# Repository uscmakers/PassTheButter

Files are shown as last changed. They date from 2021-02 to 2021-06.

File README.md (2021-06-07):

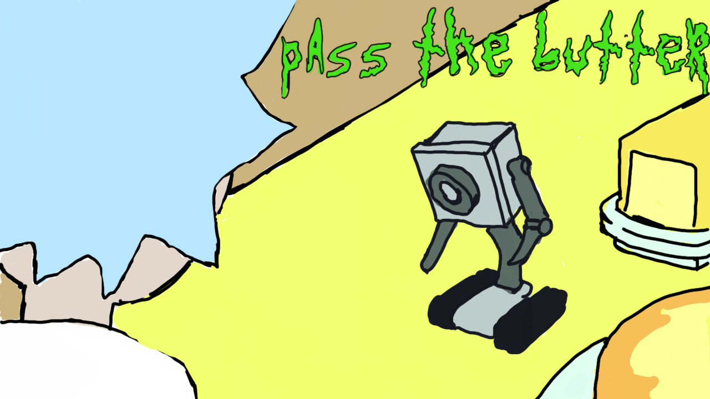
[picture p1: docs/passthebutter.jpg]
emily london logo


The purpose of this project is to build a robot which is capable of locating different people at a dinner table and passing butter to them when commanded. This is an idea made popular by a scene from Ricky and Morty.

[Here's our showcase video](https://youtu.be/vPM-rD34ycs?t=3011) describing the project, its purpose, its design, and the current state of affairs as of Spring 2021.

Full documentation can be found [here](docs/). This includes the original project plan (before work began), the bill of materials, the mechanical designs used for 3D printing, and the electronics schematics used for wiring. Electronics designs were made in [fritzing](https://fritzing.org/)

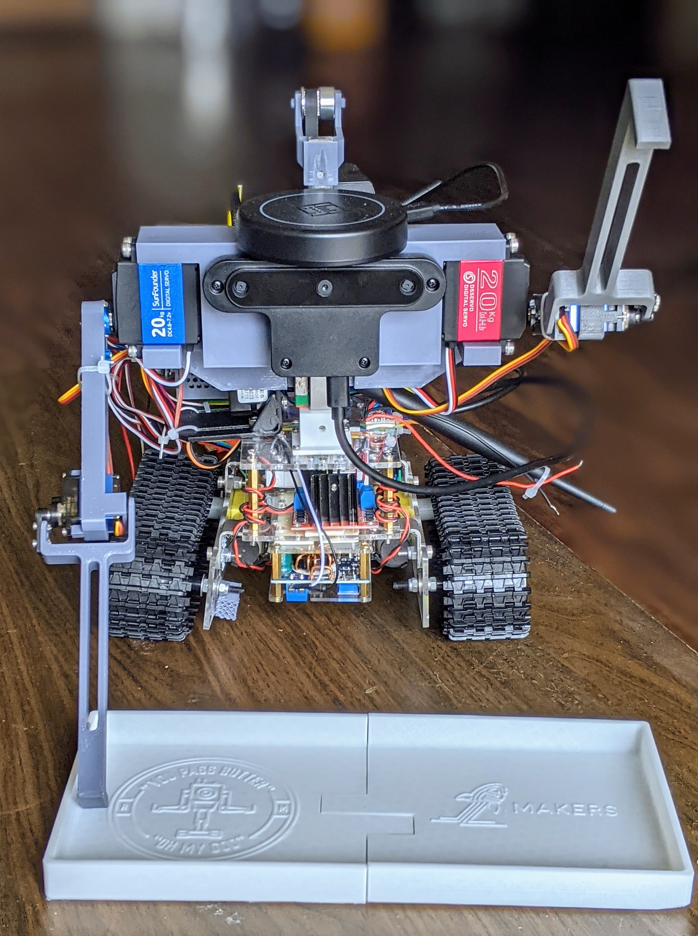
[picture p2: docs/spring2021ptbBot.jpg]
assembled robot spring 2021


# Setup

*The current version of this code expects ROS Melodic (Ubuntu 18.04) on a Jetson Nano 4GB. Many of the components will work on other platforms, but your mileage may vary, especially for things like circuit python.*

1. Wire everything up. [(See Jetson Nano pinout)](https://www.jetsonhacks.com/nvidia-jetson-nano-j41-header-pinout/)
1. [Ensure python/ROS can access your USB devices](https://askubuntu.com/questions/595896/how-to-allow-software-access-to-any-usb-devices) without admin permissions. [This may also help](https://askubuntu.com/questions/595896/how-to-allow-software-access-to-any-usb-devices).
1. [Setup circuit python on the Jetson Nano](https://learn.adafruit.com/circuitpython-libraries-on-linux-and-the-nvidia-jetson-nano/initial-setup)
1. Install ROS Melodic
1. Install pyaudio:
    ```bash
    sudo apt-get install libasound-dev portaudio19-dev libportaudio2 libportaudiocpp0
    sudo apt-get install ffmpeg libav-tools
    sudo python3 -m pip install pyaudio
    ```
1. Clone this repo to your ROS catkin_ws/src directory. 
1. `python3 -m pip install -r requirements.txt`
1. If using the wake word functionality, also do: `python3 -m pip install -r src/pass_butter/VoiceCommands/requirements.txt`
1. [Install the arduino rosserial package.](arduino/README.MD)
1. [Setup ROS for python3.](https://medium.com/@beta_b0t/how-to-setup-ros-with-python-3-44a69ca36674)
1. Build the pass_butter package with `catkin_make` or `catkin build`.

# Usage

The robot can be run in a few different ways right now, many at the same time as long as they do not use the same hardware. Take a look at the launch files and nodes especially. There remains some work to integrate all of this functionality into one or two scripts.

* If you would like to move the base around, then run this first (have it working in the background in addition to other nodes you launch): `roslaunch pass_butter arduino.launch` 
* To make the robot follow the direction of your voice run this: `rosrun pass_butter doa.py`
* To run the sequence of commands that was used for the demo video, call this `roslaunch pass_butter butter.launch`
* To view the URDF of the robot, run this: `roslaunch pass_butter rviz.launch`
* To make the robot respond to "computer" and play some response, run: `rosrun passbutter src/pass_butter/VoiceCommands/main.py --keywords computer`
* To get an interactive terminal for sending the robot commands, run this: `rosrun pass_butter demo.py`
  * 'u' - put arms up
  * 'd' - put arms down
  * 'w' - wave arms
  * 's#' - replace # with 0-4 to play different sounds
  * 'r###' - rotate the robot some amount, replace ### with a positive/negative decimal number
  * '###' - move forward or backward some amount, replace ### with a positive/negative decimal number
  * 'x' - exit/finish

## References

DOA: https://wiki.seeedstudio.com/ReSpeaker-USB-Mic-Array/#doa-direction-of-arrival

URDF: https://discourse.ros.org/t/fusion-360-add-in-to-export-urdf/6944
# Project Status

*Where does the project stand right now?*

## The Good 

1. The robot is fully assembled; the drive motors and arms are all functional. 
1. The robot has a working PID controller which is handled by an Arduino that communicates over ROS to the Jetson Nano.
1. The robot has a sense of wheel rotations and velocity thanks to the motor encoders
1. The robot can follow voice direction accurately using the directional microphone
1. The robot can respond to simple keywords such as "computer"

## The "Could Be Better"

1. Vertical head movement is non-functional. The stepper motor solution did not have enough torque to lift the relatively heavy head. The stepper motor is too weak. A worm gear motor would probably work much better with less hassle (stepper drivers can be annoying to setup).
1. The base is broken in multiple places and had to be glued back together on multiple occasions. The electronics hang off back of the base, and the base is bowing in the middle under the weight. A redesign of the base would be advisable to make it sturdier and to better fit all components.
1. The wiring is all done using a collection of breadboards and premade pcbs. This has led to some accidental short circuits of power wires. It would be much cleaner if it was all integrated to one main PCB.
1. We have an URDF to model the robot, but we do not yet have it integrated with the ROS transform system yet(e.g. [tf2](http://wiki.ros.org/tf2)) in order to view robot movement in rviz in real-time.
1. The arms do not have inverse kinematics setup--currently we work off of set points and known ranges of movement. Some calibration step would be useful too.
1. The arms can only pull or push, not grasp; more complex/useful arms would be interesting.
1. Full autonomy (obstacle avoidance, path planning) has not yet been setup/included in the software stack. The camera is currently not used.
1. Voice interaction is currently limited to wake words and does not make use of [dialogue/interaction systems](https://github.com/interaction-lab/HARMONI) which could provide much richer interactions without too much work.

# Contributors

 The project was led by a group of fantastic people who did a good amount of work in their spare time during a single semester. They are:

 * Anaka Mahesh
 * Avi Gala
 * Efaz Muhaimen (elctronics lead)
 * Max Ginsberg
 * Michael Swan (lead)
 * Misha Kuznetsov (mechanical lead)
 * Sam Jeon (autonomy lead)
 * Sarah Parks
 * Spencer Lin (voice interaction lead)

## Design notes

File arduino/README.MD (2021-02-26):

# Install Instructions

1. Install Arduino IDE
2. Get ROS Arduino libraries and install for ROS and Arduino:
```bash
sudo apt-get update
sudo apt-get install ros-melodic-rosserial-arduino
cd ~/Arduino/libraries
rosrun rosserial_arduino make_libraries.py .
```
3. Flash Arduino with provided code.
4. Start ros and run serial node communication (replace /dev/tty... with path matching your Arduino)
```bash
roscore
rosrun rosserial_python serial_node.py /dev/ttyACM0
```
5. Publish updates to the Arduino using ROS, e.g. `rostopic pub /servo std_msgs/UInt16 "data: 180"`

# References
http://wiki.ros.org/rosserial_arduino/Tutorials/Arduino%20IDE%20Setup

http://wiki.ros.org/rosserial_arduino/Tutorials/Blink

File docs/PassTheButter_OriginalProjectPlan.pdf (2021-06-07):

### Project Plan

1. Give a title for this project. (This can change later) Pass the Butter!
2. Describe the project in 2-3 sentences.

Build a robot which is capable of locating different people at a dinner table and passing butter to them when commanded. This is an idea made popular by a scene from Ricky and Morty. (https://youtu.be/X7HmltUWXgs?t=32) A toy is being produced (https://www.thebutterrobot.com/) for a similar purpose, but ours should be more customizable.

3. List the subsystems for this project and specify what each group will deliver by the end of the project.

Core subsystems
- Speaking: Shout out fun phrases when the robot engages in different actions.
- Listening: Listen to people and activate actions (e.g. passing butter) when certain key words are spoken. This subsystem must also provide the direction of spoken words (microphone arrays can do this).
- Butter Passing: Using either passive or active actuation, move butter around the table.
- Driving: Provide wheels, frame, and motors for rover to drive around upon. This can be done from scratch or by assembling a kit; that decision depends on available team members and interests.
- Obstacle Avoidance/Pathfinding: Avoid obstacles on the table and keep from falling off the table.

Possible extensions
- Conversing: Use Natural Language Understanding (NLU) to engage in a full conversation with people.
- Teleoperating: Control the robot and view its camera remotely using a computer, phone, or even Twitch chat. (https://www.twitch.tv/twitchplayspokemon)
- Voice Recognition: Identity the speaker using their voice, and then respond differently to different voices.
- Face Recognition: Same as voice recognition, except using faces.
- XYZ Passing: Pickup and move around other things (plates, trash, utensils, etc.) besides butter
4. How many people do you think you need on your team? Mention roles and skills if possible.

6-8 people, myself included (I fall into both the Computer/Software Engineer roles). We can support more software engineers (up to 6) if there are extra people available.

- 1-2 Mechanical Engineers to focus on robot body design/3D printing, motor placement, and actuator design for driving and butter passing.
- 2 Electrical/Computer Engineers to handle power distribution/wiring/pcb design and possibly help with some programming work.
- 3-4 Software Engineers to integrate and control all subsystems, with the bulk of their work being divided among the listening and obstacle avoidance subsystems.
5. List out parts your project will need, along with links for where to order them from.
a. [Already purchased] OAK-D AI + Depth Camera: https://www.kickstarter.com/projects/opencv/opencv-ai-kit
b. Speaker:
https://www.amazon.com/dp/B087D2BPBC/ref=cm_sw_em_r_mt_dp_6C T.FbAHCDT44 (https://www.amazon.com/dp/B087D2BPBC/ref=cm_sw_em_r_mt_dp_6CT.FbAHCDT44)
c. Microphone array (directional audio): https://www.digikey.com/short/477r2v
OR
https://www.seeedstudio.com/ReSpeaker-USB-Mic-Array-p-4247.html
d. Jetson nano:
https://www.amazon.com/dp/B084DSDDLT/ref=cm_sw_em_r_mt_dp_2I T.FbE0Y5RNH (https://www.amazon.com/dp/B084DSDDLT/ref=cm_sw_em_r_mt_dp_2IT.FbE0Y5RNH)
e. WiFi for Jetson nano:
https://www.amazon.com/dp/B07V9B5C6M/ref=cm_sw_em_r_mt_dp_oJ T.Fb4XAX22R (https://www.amazon.com/dp/B07V9B5C6M/ref=cm_sw_em_r_mt_dp_oJT.Fb4XAX22R)
f. Micro sd card:
https://www.amazon.com/dp/B08879MG33/ref=cm_sw_em_r_mt_dp_g5 T.FbC1ADJK3 (https://www.amazon.com/dp/B08879MG33/ref=cm_sw_em_r_mt_dp_g5T.FbC1ADJK3)
g. Jetson fan:
https://www.amazon.com/dp/B071FNHVXN/ref=cm_sw_em_r_mt_dp_85 T.FbS3C6MND (https://www.amazon.com/dp/B071FNHVXN/ref=cm_sw_em_r_mt_dp_85T.FbS3C6MND)
h. Jetson test bench Power Supply: https://www.amazon.com/dp/B07413Q5Y4
i. [Many Options, Choose 1] Motors + motor driver + chassis:
i. Jetbot kit https://www.adafruit.com/product/4225
ii. Tank Tread kit: https://smile.amazon.com/dp/B08F23SDF5/ref=cm_sw_em_r_mt_ dp_ZSJaGbBWMGKRD (https://smile.amazon.com/dp/B08F23SDF5/ref=cm_sw_em_r_mt_dp_ZSJaGbBWMGKRD)

iii. | Elegoo Kit
| https://smile.amazon.com/dp/B07KPZ8RSZ/ref=cm_sw_em_r_mt_
| dp_dlT1_rTJaGbBSVW61Z?_encoding=UTF8&psc=1 (https://smile.amazon.com/dp/B07KPZ8RSZ/ref=cm_sw_em_r_mt_dp_dlT1_rTJaGbBSVW61Z?_encoding=UTF8&psc=1)
iv. | Tank with arm kit:
| https://smile.amazon.com/dp/B07Q3RQCQS/ref=cm_sw_em_r_mt
| _dp_UTJaGbGKZDVG3 (https://smile.amazon.com/dp/B07Q3RQCQS/ref=cm_sw_em_r_mt_dp_UTJaGbGKZDVG3)
v. Osoyoo kit:
| https://smile.amazon.com/dp/B08JLS3J7Q/ref=cm_sw_em_r_mt_
| dp_AUJaGb61WHR82 (https://smile.amazon.com/dp/B08JLS3J7Q/ref=cm_sw_em_r_mt_dp_AUJaGb61WHR82)
vi. | 3-layer kit: https://www.adafruit.com/product/3244
j. Battery + regulators:
https://forums.developer.nvidia.com/t/power-supply-considerations-for-jetson-nano-developer-kit/71637/245 (https://forums.developer.nvidia.com/t/power-supply-considerations-for-jetson-nano-developer-kit/71637/245)
i. Most likely option: 2s LiPo battery with motor drivers provided by
| kit and possibly a 5V regulator and/or separate battery for the
| jetson; I already have a 2s LiPo
ii. | 5V Regulator (can work for servos and/or Jetson):
| https://www.amazon.com/dp/B00C63TLCC/ref=cm_sw_em_r_mt_
| dp_zvKaGbWTP4BB2 (https://www.amazon.com/dp/B00C63TLCC/ref=cm_sw_em_r_mt_dp_zvKaGbWTP4BB2)
k. Table edge detection (if not in kit): https://www.amazon.com/dp/B00XT0PBC0/ref=cm_sw_em_r_mt_dp_eb KaGbQN4BDSX (https://www.amazon.com/dp/B00XT0PBC0/ref=cm_sw_em_r_mt_dp_ebKaGbQN4BDSX)
l. Robot arm servos (MG90S): https://www.amazon.com/dp/B07FLXZ1VK/ref=cm_sw_em_r_mt_dp_lqK aGbN11ACJW (https://www.amazon.com/dp/B07FLXZ1VK/ref=cm_sw_em_r_mt_dp_lqKaGbN11ACJW)
m. Robot arm gripper: https://www.pololu.com/product/3551
6. Layout a timeline of the milestones that need to be completed to finish the project. Expect there to be 10-11 productive weeks to complete the project.
- Mid February: Robot prototype assembled and motors moving
- Mid March:
- Majority of mechanical/electrical body design/assembly (except arms) completed
- Table edge detection working
- Speaker working
- Mid April:
- Arms functional
- Microphone able to determine audio direction
- Obvious obstacles autonomously avoided using camera
- May (final): Able to pass butter from one side of table to the other using voice commands.

Embedded Plans/Considerations
- [Efaz] Using Fritzing for system connection diagram
- Don’t worry about circuit diagrams as much unless we add more small components
- 2 Arduino nanos, one for arms/servos, another for locomotion
- Arduinos communicate with Jetson Nano over serial (rosserial package)
- IMU contacts arduino over I2C

Jetson Nano Software Plans/Considerations:
- LucidChart for software package diagram: https://lucid.app/lucidchart/invitations/accept/1264b90b-86f0-4d57-a3e3-5235 82440beb (https://lucid.app/lucidchart/invitations/accept/1264b90b-86f0-4d57-a3e3-523582440beb)
- 30deg separation difference minimum needed for ultrasonic sensor to avoid interference
- Simplify arm IK by just doing it ourselves instead of integrating MoveIt: https://youtu.be/IN8tjTk8ExI
- What is the max speed we will set for our robot?

Mechanical Ideas/Plans:
- Linear rail MGN12 H (150 mm) for vertical cam movement provided by Spencer: https://www.aliexpress.com/item/32806622073.html?spm=a2g0s.9042311.0.0.27 424c4dN0Uh1O
- Using black micro servos for arms.
- 2 arms if possible, but otherwise only one.
- Could get higher torque even: https://www.adafruit.com/product/2307
- Gripper for arm that uses micro servo: https://www.pololu.com/product/3551
- Potential drive train depends on size of nano + other parts
- https://www.amazon.com/dp/B08F23SDF5/ref=cm_sw_em_r_mt_dp_ZSJaGbBWMGKRD?pldnSite=1 (https://www.amazon.com/dp/B08F23SDF5/ref=cm_sw_em_r_mt_dp_ZSJaGbBWMGKRD?pldnSite=1)
- https://www.amazon.com/DGJYT-Preminum-Raspberry-Learning-Caterpillar/dp/B08HSTC96H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 (https://www.amazon.com/DGJYT-Preminum-Raspberry-Learning-Caterpillar/dp/B08HSTC96H)
- https://www.amazon.com/Experiment-Programable-Platform-Compatible-Raspberry/dp/B0892YJ3KQ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 psc=1&refRID=W7JTG1CQZ3TFHQY6RTX0 (https://www.amazon.com/Experiment-Programable-Platform-Compatible-Raspberry/dp/B0892YJ3KQ)

- Could consider 3D printing something from Thingiverse
■ https://www.thingiverse.com/thing:2024364
■
- Motors with encoders: https://www.dfrobot.com/product-1457.html
- Max’s servo:
https://www.amazon.com/SunFounder-Waterproof-SF3218MG-Digital-Aluminium/dp/B07VJG5QTJ (https://www.amazon.com/SunFounder-Waterproof-SF3218MG-Digital-Aluminium/dp/B07VJG5QTJ)
- Micro servos:
- https://www.adafruit.com/product/2307
- https://www.adafruit.com/product/1143 ●

●

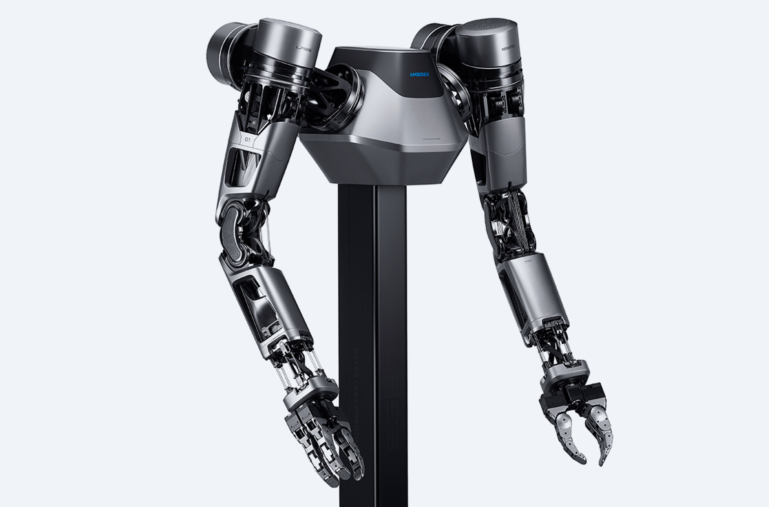
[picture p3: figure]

Reference Projects
1. Cliff detection and collision avoidance using IR sensors
- https://www.youtube.com/watch?v=d7J0Bb78y2s
- https://www.youtube.com/watch?v=BLYP94Yk12U
- https://www.youtube.com/watch?v=lN9uT30YzAg
●

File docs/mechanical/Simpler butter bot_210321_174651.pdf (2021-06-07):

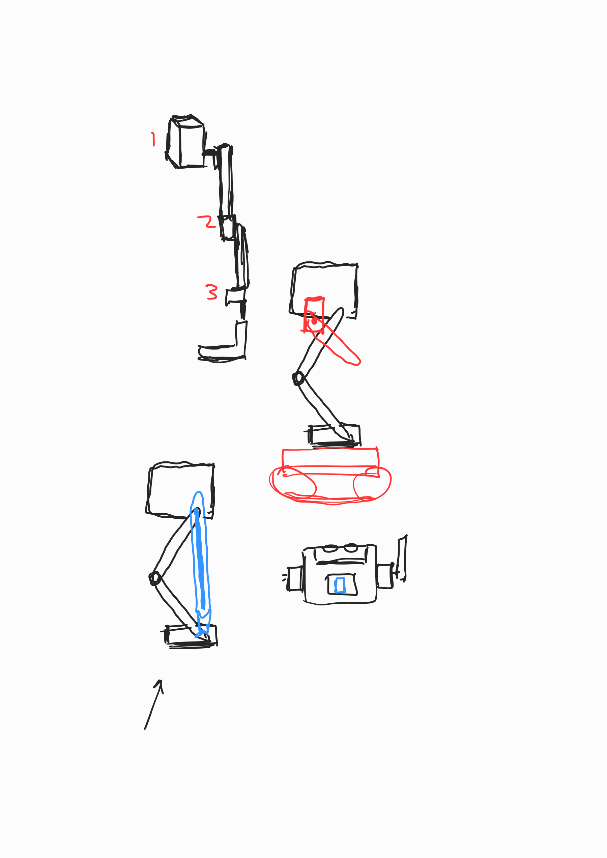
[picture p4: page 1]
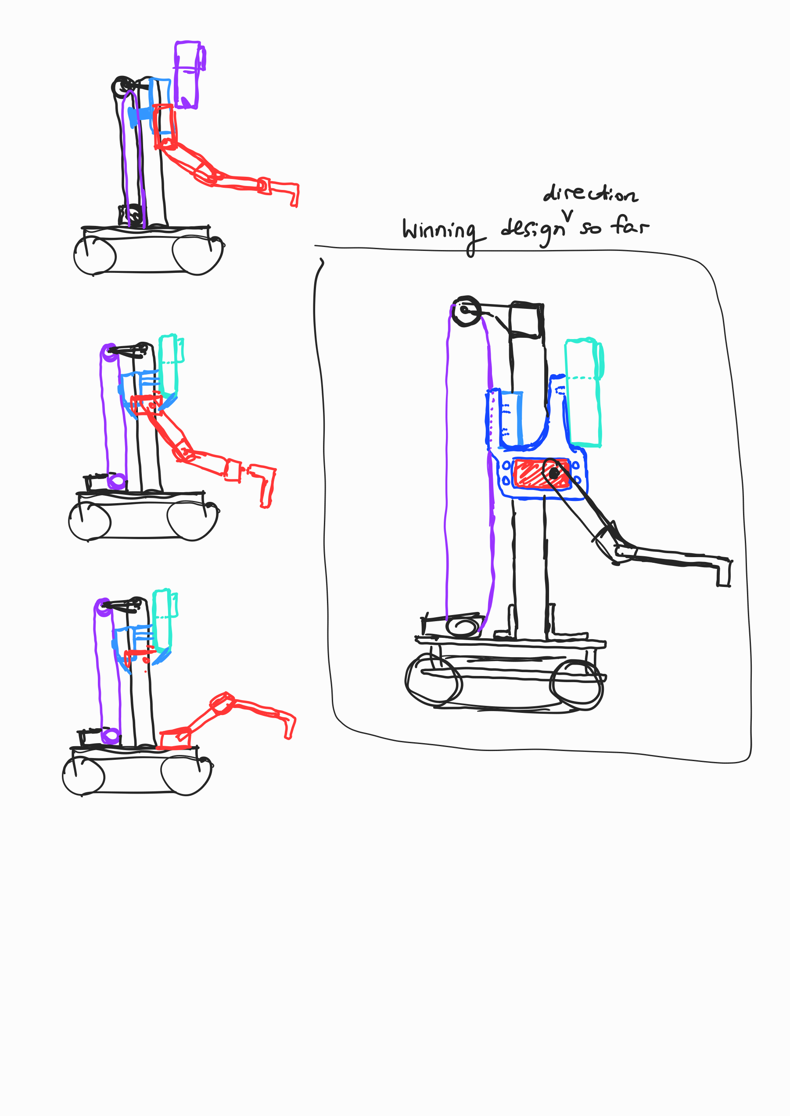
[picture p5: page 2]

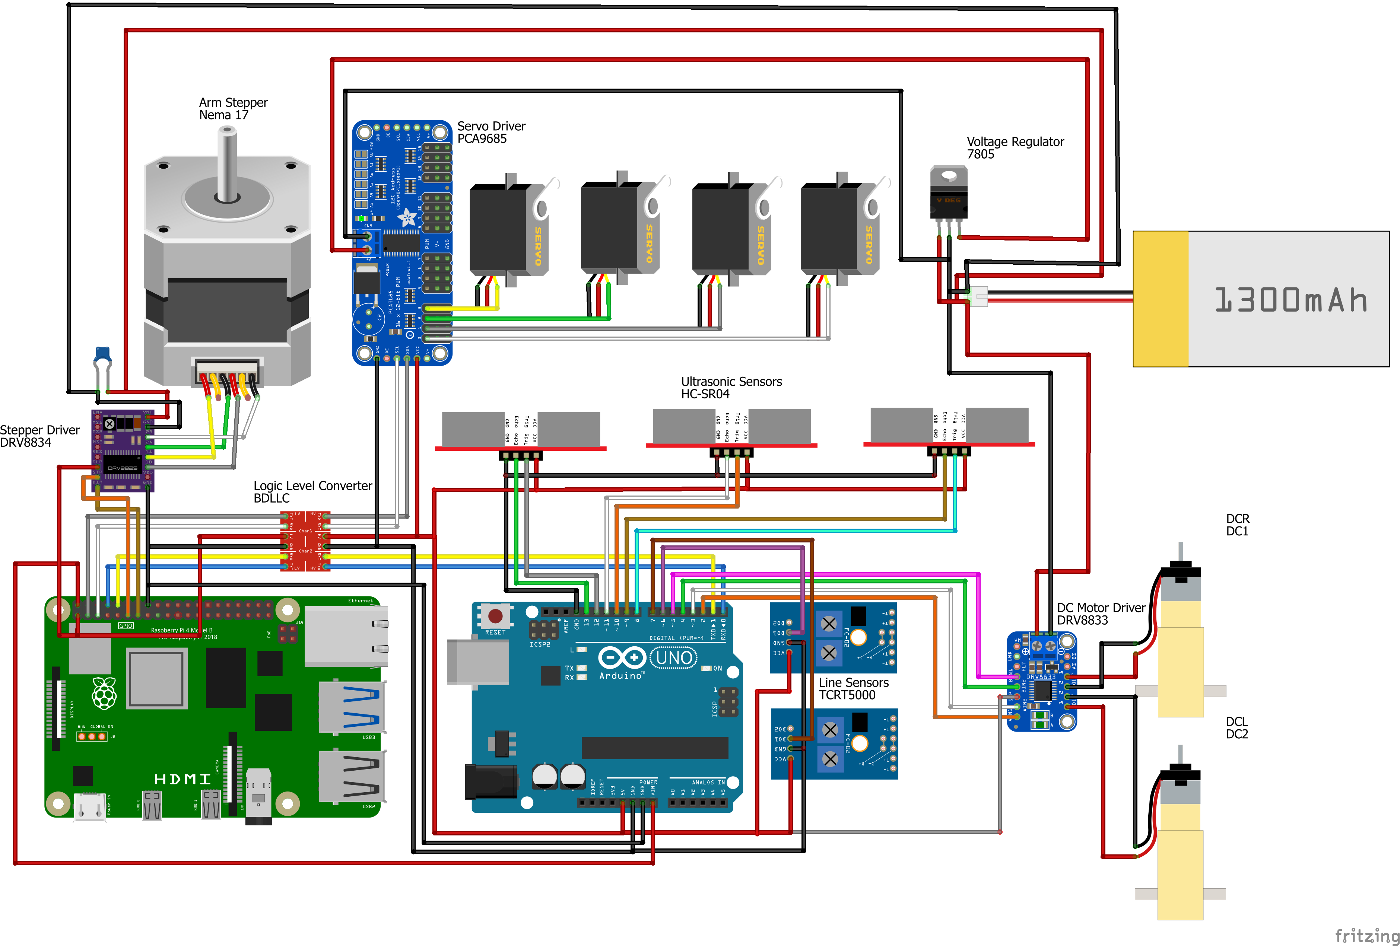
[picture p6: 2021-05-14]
docs/electronics/Schematic.png

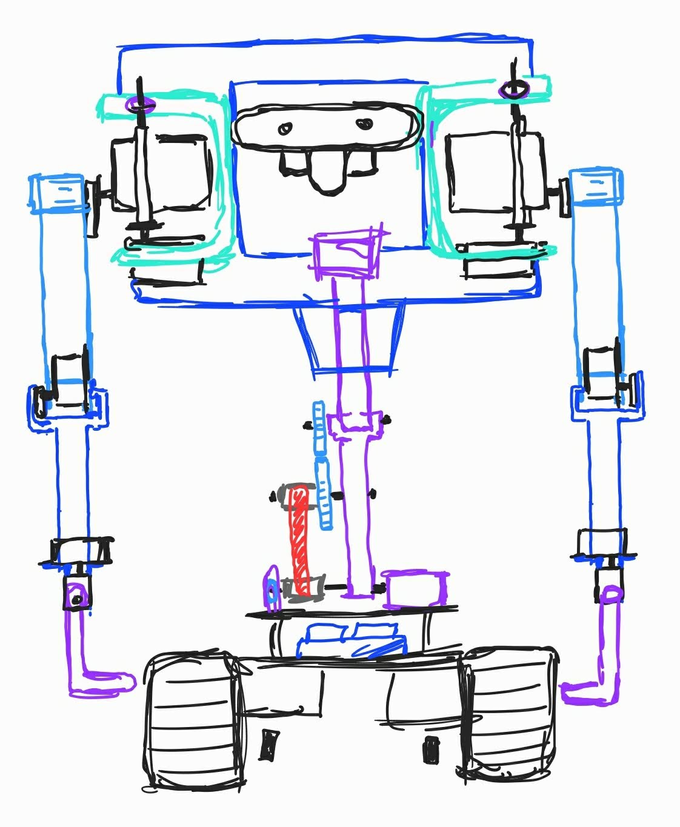
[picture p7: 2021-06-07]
docs/mechanical/SmartSelect_20210307-023447_Samsung Notes.jpg

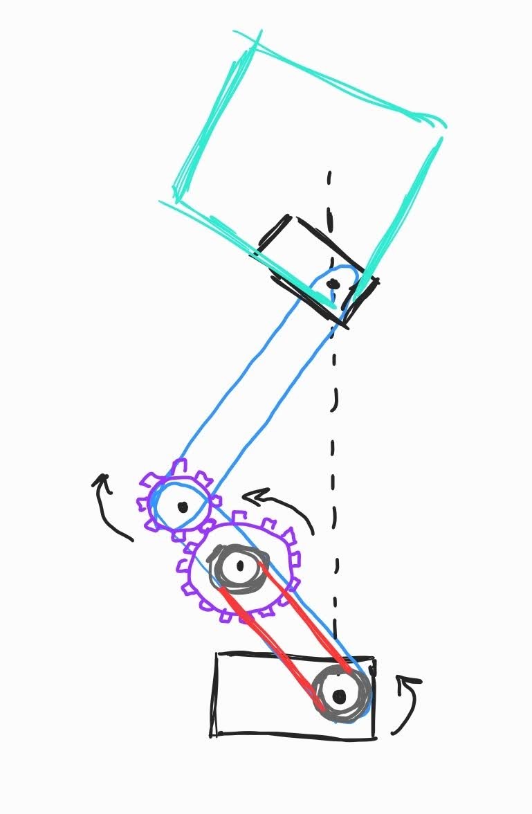
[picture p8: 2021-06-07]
docs/mechanical/SmartSelect_20210307-014712_Samsung Notes.jpg

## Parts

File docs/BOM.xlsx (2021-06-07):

Category | State | Part Name | Part Description | Make/Buy | QTY | Unit Cost | Shipping | Cost (excl tax + shipping) | Final Cost (incl tax + shipping)) | Vendor | Vendor URL | Comments
Electronics | Purchased | Jetson Nano 4GB |  |  | 1 | $84.99 | Prime - free | $84.99 | $93.06 |  | https://www.amazon.com/dp/B084DSDDLT/ref=cm_sw_em_r_mt_dp_7MWT5MMYDYXTCAPRW6YM
Electronics | Purchased | Jetson Nano Wifi Adapter |  |  | 1 | $24.25 | Prime - free | $24.25 | $26.55 |  | https://www.amazon.com/dp/B07V9B5C6M/ref=cm_sw_em_r_mt_dp_oJT.Fb4XAX22R
Electronics | Purchased | Noctua NF-A4x20 5V PWM | Fan for Jetson Nano |  | 1 | $14.95 | Prime - free | $14.95 | $16.37 |  | https://www.amazon.com/dp/B071FNHVXN/ref=cm_sw_em_r_mt_dp_85T.FbS3C6MND
Electronics | Purchased | 64 gb microSD card | for Jetson Nano |  | 1 | $10.99 | Prime - free | $10.99 | $12.03 |  | https://www.amazon.com/dp/B08879MG33/ref=cm_sw_em_r_mt_dp_g5T.FbC1ADJK3
Electronics | Purchased | Geekworm DC 5V 4A Power Adapter | AC Power supply for Nano |  | 1 | $17.99 | Prime - free | $17.99 | $19.70 |  | https://www.amazon.com/dp/B07413Q5Y4
Electronics | Have | Ultrasonic Sensor |  |  | 1 set (3 pieces) | $7.99 | Prime - free | $7.99 | $8.75 |  | https://www.amazon.com/Excelity-Ultrasonic-HC-SR04-Distance-Mounting/dp/B07SC1YJ21
Electronics | Tentative | Infrared Sensor |  |  | 1 set (5 pieces) | $5.49 | Prime - free | $5.49 | $6.01 |  | https://www.amazon.com/dp/B00XT0PBC0/ref=cm_sw_em_r_mt_dp_ebKaGbQN4BDSX
Electronics | Have | Motor+Encoder |  |  | 2 | $7.40 |  | $14.80 | $16.20 |  | https://www.dfrobot.com/product-1457.html
Mechanical | Purchased | 6Pcs MG90S Micro Servo |  |  | 1 set (6 pcs) | $18.99 | Prime - free | $18.99 | $20.79 | amazon | https://www.amazon.com/Seamuing-MG90S-Micro-Geared-Helicopter/dp/B07F7VJQL5/
 |  |  |  |  |  |  |  | $0.00 | $0.00
Mechanical | Purchased | Higher torque micro servo |  |  | 2 | $11.95 | $5.10 | $23.90 | $31.27 |  | https://www.adafruit.com/product/2307
Mechanical | Purchased | Drive Base |  |  | 1 | $27.90 | Prime - free | $27.90 | $30.55 | amazon | https://www.amazon.com/dp/B08F23SDF5/ref=cm_sw_em_r_mt_dp_ZSJaGbBWMGKRD?pldnSite=1
Mechanical | Purchased | 2 20KG Servo |  |  | 1 set (2 pcs) | $30.99 | Prime - free | $30.99 | $33.93 |  | https://www.amazon.com/DS3218-Digital-Servo-Torque-Waterproof/dp/B07TKTQ2NZ
Electronics | Have | Arduinos |  |  | 1 set (3 pcs)
Electronics | Purchased | DRV8833 DC Motor Driver |  |  | 1 | $8.91 | Prime - free | $8.91 | $9.76 |  | https://www.amazon.com/Adafruit-DRV8833-Stepper-Driver-Breakout/dp/B01MFE1CZU/
Electronics | Purchased | ReSpeaker USB Mic Array |  |  | 1 | $69.00 | $6.32 | $69.00 | $75.32 |  | https://www.seeedstudio.com/ReSpeaker-USB-Mic-Array-p-4247.html
Electronics | Purchased | USB Speaker |  |  | 1 | $19.99 | Prime - free | $19.99 | $21.89 |  | https://www.amazon.com/dp/B087D2BPBC/ref=cm_sw_em_r_mt_dp_6CT.FbAHCDT44
Electronics | Purchased | Diymore 6DOF MPU-6050 |  |  | 1 | $6.90 | Prime - free | $6.90 | $7.55 |  | https://www.amazon.com/dp/B01J167T84/ref=cm_sw_em_r_mt_dp_B9NT7TBK1H0HZQJKAH9Y?_encoding=UTF8&psc=1
Electronics | Purchased | Logic Level Converter |  |  | 1 | $7.49 | Prime - free | $7.49 | $8.20 |  | https://www.amazon.com/HiLetgo-Channels-Converter-Bi-Directional-3-3V-5V/dp/B07F7W91LC/
Mechancial | Purchased | Stepper Motor Nema 17 |  |  | 1 | $9.99 | Prime - free | $9.99 | $10.94 | amazon | https://www.amazon.com/Twotrees-Stepper-17HS4401-Connector-Printer/dp/B07TGJSNJB
Mechanical | Purchased | Stepper Motor Bracket |  |  | 1 | $5.99 | Prime - free | $5.99 | $6.56 | amazon | https://www.amazon.com/STEPPERONLINE-Mounting-Bracket-Stepper-Printer/dp/B00Q6F51C0
Mechancial | Purchased | Pulleys |  |  | 1 | $8.98 | Prime - free | $8.98 | $9.83 | amazon | https://www.amazon.com/gp/product/B077GNZK3J/ref=ppx_yo_dt_b_search_asin_title?ie=UTF8&th=1
Mechancial | Purchased | Belts |  |  | 1 | $10.99 | Prime - free | $10.99 | $12.03 | amazon | https://www.amazon.com/Houkr-Printer-Timing-Closed-Perimeter/dp/B085NMDTDM
Electronics | Purchased | Voltage Regulator |  |  | 1 | $13.99 | Prime - free | $13.99 | $15.32 |  | https://www.amazon.com/AITRIP-Adjustable-Regulator-Transformer-Converter/dp/B08FJ2GGQN/
Electronics | Purchased | Servo Driver |  |  | 1 | $9.99 | Prime - free | $9.99 | $10.94 |  | https://www.amazon.com/SunFounder-PCA9685-Channel-Arduino-Raspberry/dp/B014KTSMLA/
Electronics | Purchased | Stepper Driver |  |  | 1 | $5.95 | $4.33 | $5.95 | $10.84 | Pololu | https://www.pololu.com/product/2134
Electronics | tentative | Voltage Sensor |  |  | 1 | $13.74 | Prime - free | $13.74 | $15.04 |  | https://www.amazon.com/Adafruit-INA260-Voltage-Current-Sensor/dp/B07S8QYDF8/
Electronics | Have | OAK-D Camera |  |  | 1 | $149 | $16 | $149 | $165.00 |  | https://store.opencv.ai/products/oak-d
Mechanical | Have | MGN 12H 150mm Linear Rail |  |  | 1 | $10.13 |  |  |  |  | https://www.aliexpress.com/item/32806622073.html?spm=a2g0s.9042311.0.0.27424c4dN0Uh1O
 |  |  |  |  |  |  |  |  | Purchased so far
 |  |  |  |  |  |  |  |  | $483.42
 |  |  |  |  |  |  |  |  | Everything Total
 |  |  |  |  |  |  |  |  | $694.43

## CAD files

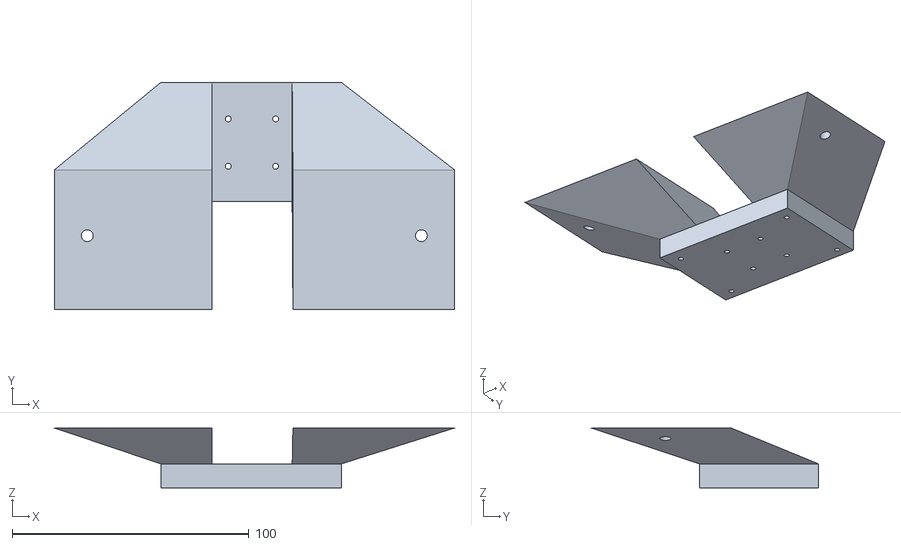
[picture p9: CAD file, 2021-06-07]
docs/mechanical/body2mmholes.stl
168.8 x 95.9 x 25.3

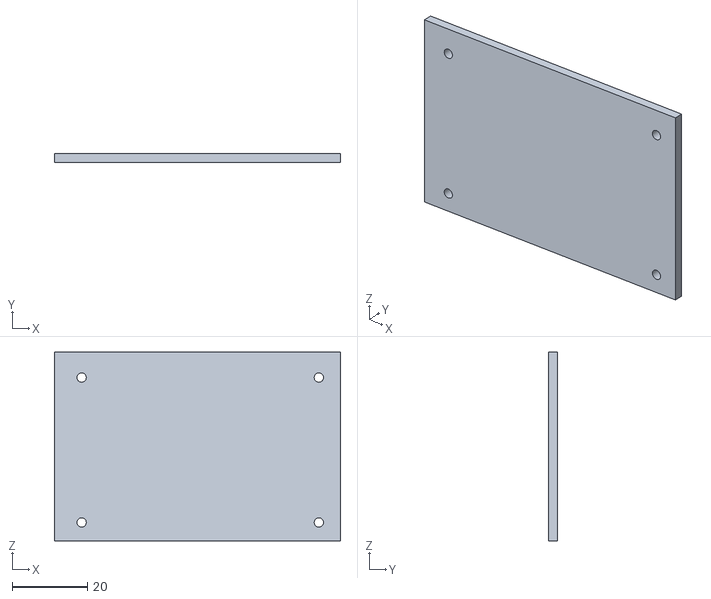
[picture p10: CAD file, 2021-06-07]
docs/mechanical/body3mmholes.stl
76.2 x 2.34 x 50.3

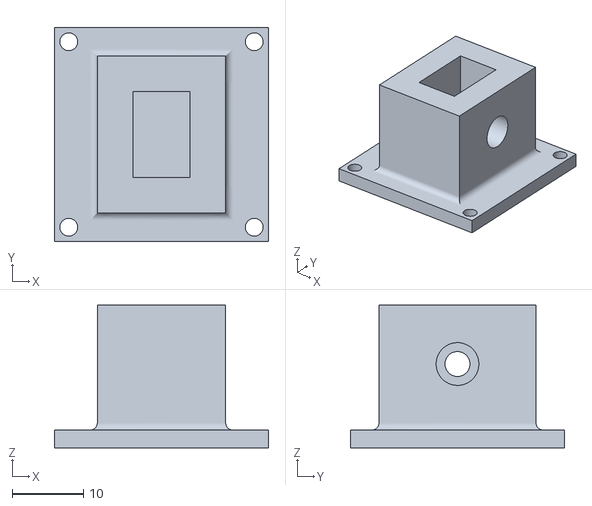
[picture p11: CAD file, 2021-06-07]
docs/mechanical/Bracket v1.stl
30.0 x 30.0 x 20.0

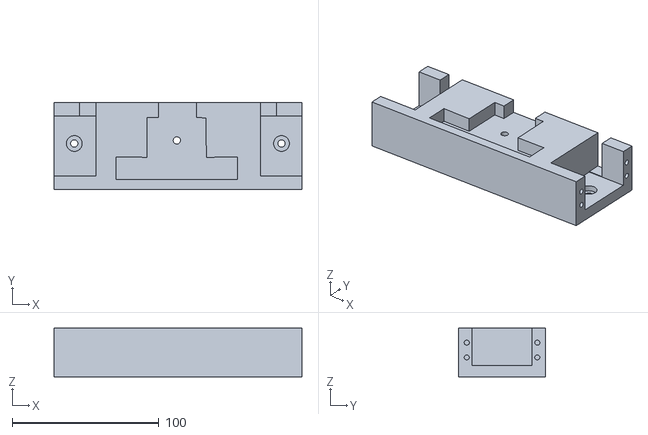
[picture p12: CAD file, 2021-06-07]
docs/mechanical/bigboyholes.stl
168.8 x 59.0 x 33.0

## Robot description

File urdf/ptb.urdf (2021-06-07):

<?xml version="1.0"?>
<robot name="test_robot">

  <link name="base_link">
    <visual>
      <geometry>
        <box size="0.5 0.3 0.05"/>
      </geometry>
      <origin rpy="0 0 0" xyz="0 0 0.085"/>
      <material name="white">
        <color rgba="1 1 1 1"/>
      </material>
    </visual>
  </link>
  
  <link name="lfwheel">
    <visual>
      <geometry>
        <cylinder length="0.008" radius="0.046"/>
      </geometry>
      <origin rpy="1.5708 0 0" xyz="0 0 0"/>
      <material name="black">
        <color rgba="0 0 0 1"/>
      </material>
    </visual>
  </link>
  
  <joint name="base_to_lfwheel" type="continuous">
    <parent link="base_link"/>
    <child link="lfwheel"/>
    <axis rpy="0 0 0" xyz="0 1 0"/>
    <origin xyz=".2 0.16 0.046" rpy="0 0 0"/>
  </joint>
  

 <link name="lbwheel">
    <visual>
      <geometry>
        <cylinder length="0.008" radius="0.046"/>
      </geometry>
      <origin rpy="1.5708 0 0" xyz="0 0 0"/>
      <material name="black">
        <color rgba="0 0 0 1"/>
      </material>
    </visual>
  </link>
  
  <joint name="base_to_lbwheel" type="continuous">
    <parent link="base_link"/>
    <child link="lbwheel"/>
    <axis rpy="0 0 0" xyz="0 1 0"/>
    <origin xyz="-.2 0.16 0.046" rpy="0 0 0"/>
  </joint>
  

  <link name="rfwheel">
    <visual>
      <geometry>
        <cylinder length="0.008" radius="0.046"/>
      </geometry>
      <origin rpy="1.5708 0 0" xyz="0 0 0"/>
      <material name="black">
        <color rgba="0 0 0 1"/>
      </material>
    </visual>
  </link>
  
  <joint name="base_to_rfwheel" type="continuous">
    <parent link="base_link"/>
    <child link="rfwheel"/>
    <axis rpy="0 0 0" xyz="0 1 0"/>
    <origin xyz= ".2 -0.16 0.046" rpy="0 0 0"/>
  </joint>

 <link name="rbwheel">
    <visual>
      <geometry>
        <cylinder length="0.008" radius="0.046"/>
      </geometry>
      <origin rpy="1.5708 0 0" xyz="0 0 0"/>
      <material name="black">
        <color rgba="0 0 0 1"/>
      </material>
    </visual>
  </link>
  
  <joint name="base_to_rbwheel" type="continuous">
    <parent link="base_link"/>
    <child link="rbwheel"/>
    <axis rpy="0 0 0" xyz="0 1 0"/>
    <origin xyz="-.2 -0.16 0.046" rpy="0 0 0"/>
  </joint>

  <link name="post">
    <visual>
      <geometry>
        <box size=".03 .03 .4"/>
      </geometry>
      <origin rpy="0 0 0" xyz="0 0 .2"/>
      <material name="black">
        <color rgba="0 0 0 1"/>
      </material>
    </visual>
  </link>

  <joint name="post_to_chassis" type="fixed">
    <parent link="base_link"/>
    <child link="post"/>
    <origin xyz=".2 0 .1" rpy="0 0 0"/>
  </joint>
 
  <link name="cross">
    <visual>
      <geometry>
        <box size=".03 .3 .03"/>
      </geometry>
      <origin rpy="0 0 0" xyz="0 0 0"/>
      <material name="black">
        <color rgba="0 0 0 1"/>
      </material>
    </visual>
  </link>

  <joint name="cross_to_post" type="prismatic">
    <parent link="post"/>
    <child link="cross"/>
    <axis xyz="0 0 1"/>
     <limit effort="1000.0" lower="-.2" upper="0" velocity="0.5"/>
    <origin xyz="0 0 .3" rpy="0 0 0"/>
  </joint>



  <link name="upper_arm_l">
    <visual>
      <geometry>
        <box size=".15 .03 .03"/>
      </geometry>
      <origin rpy="0 0 0" xyz=".05 0 0"/>
      <material name="white">
        <color rgba="0 0 0 0"/>
      </material>
    </visual>
  </link>

  <joint name="upper_arm_l_to_cross" type="revolute">
    <parent link="cross"/>
    <child link="upper_arm_l"/>
    <axis xyz="0 1 0"/>
    <limit effort="1000.0" lower="0.0" upper="-0.7" velocity="0.5"/>
    <origin xyz="0 .17 0" rpy="0 0 0"/>
  </joint>

  <link name="forearm_l">
    <visual>
      <geometry>
        <box size=".15 .03 .03"/>
      </geometry>
      <origin rpy="0 0 0" xyz="0.06 0 0"/>
      <material name="black">
        <color rgba="0 0 0 1"/>
      </material>
    </visual>
  </link>

  <joint name="forearm_l_to_upper_arm_l" type="revolute">
    <parent link="upper_arm_l"/>
    <child link="forearm_l"/>
    <axis xyz="0 1 0"/>
   <limit effort="1000.0" lower="0.0" upper="-0.7" velocity="0.5"/>
    <origin xyz=".1 .035 0" rpy="0 0 0"/>
  </joint>

  <link name="upper_arm_r">
    <visual>
      <geometry>
        <box size=".15 .03 .03"/>
      </geometry>
      <origin rpy="0 0 0" xyz=".05 0 0"/>
      <material name="white">
        <color rgba="0 0 0 0"/>
      </material>   
    </visual>
  </link>

  <joint name="upper_arm_r_to_cross" type="revolute">
    <parent link="cross"/>
    <child link="upper_arm_r"/>
    <axis xyz="0 1 0"/>
    <limit effort="1000.0" lower="0.0" upper="-0.7" velocity="0.5"/>
    <origin xyz="0 -.17 0" rpy="0 0 0"/>
  </joint>

  <link name="forearm_r">
    <visual>
      <geometry>
        <box size=".15 .03 .03"/>
      </geometry>
      <origin rpy="0 0 0" xyz=".06 0 0"/>
      <material name="black">
        <color rgba="0 0 0 1"/>
      </material>
    </visual>
  </link>

  <joint name="forearm_r_to_upper_arm_r" type="revolute">
    <parent link="upper_arm_r"/>
    <child link="forearm_r"/>
    <axis xyz="0 1 0"/>
    <limit effort="1000.0" lower="0.0" upper="-0.7" velocity="0.5"/>
    <origin xyz=".1 -.035 0" rpy="0 0 0"/>
  </joint>
  
</robot>

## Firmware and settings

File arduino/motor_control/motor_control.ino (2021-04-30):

#include <PID_v1.h> // PID library
#include <ros.h> // ROS serial
#include <ros/time.h>
#include "Wire.h" // IMU wire library
#include "I2Cdev.h"
#include <geometry_msgs/Vector3.h> 
#include <tf/transform_broadcaster.h>
#include <MPU6050.h> // MPU 6050 IMU library

MPU6050 mpu;

//Create an object that represents the ROS node
ros::NodeHandle nh;

//Create sensor messages
geometry_msgs::TransformStamped t; 
geometry_msgs::TransformStamped t2;
tf::TransformBroadcaster broadcaster;

//Encoders
const byte encoder0pinA = 2;// A pin for motor 1
const byte encoder0pinB = 4;// B pin for motor 1

const byte encoder1pinA = 3;// A pin for motor 2
const byte encoder1pinB = 5;// B pin for motor 2

byte encoder0PinALast; // Last encoder reading for motor 1
byte encoder1PinALast; // Last encoder reading for motor 2

double duration1; // Pulses/sec for the encoder in motor 1
double duration2; // Pulses/sec for the encoder in motor 2

double abs_duration1, abs_duration2; // Speed for motor 1 and 2

//Motor PWM
double PWM1, PWM2; // PWM signals for motor 1 and motor 2

double set1, set2 = 0; // Velocity set points for motor 1 and motor 2
double setanglespeed; // Angular speed set point
double setspeed; // Net speed

int r = 0.035; // Wheel radius (m)
int l = 0.11 ; // Robot track width (m)

boolean Direction1; // Motor 1 direction
boolean Direction2; // Motor 2 direction

const int ENA = 6; // Motor1 output pin
const int IN1 = 7; // Motor1 direction pin 1
const int IN2 = 8; // Motor1 direction pin 2

const int ENB = 11; // Motor2 output pin
const int IN3 = 9; // Motor2 direction pin 1
const int IN4 = 10; // Motor2 direction pin 2

//IMU
float yaw, yawRate,xAcc,yAcc = 0;
float timeStep = 0.01;

float read1 = 0;
float read2 = 0;

char world[] = "world";
char imu[] = "/imu";


// Timers
unsigned long timer, range_timer = 0;

double set = 0; // Setpoint speed -- I guess will be given order from ROS
double val_output; // PWM output
double Kp=0.6, Ki=3.8, Kd=0; // PID gains
PID myPID1(&abs_duration1, &PWM1, &set1, Kp, Ki, Kd, DIRECT); // PID setup for motor 1
PID myPID2(&abs_duration2, &PWM2, &set1, Kp, Ki, Kd, DIRECT); // PID setup for motor 1
boolean result1, result2; // PID control outcome

void setup()
{
  nh.initNode();
  broadcaster.init(nh); 

  // Initialize MPU6050
  while(!mpu.begin(MPU6050_SCALE_2000DPS, MPU6050_RANGE_2G))
  {
    Serial.println("Could not find a valid MPU6050 sensor, check wiring!");
    delay(500);
  }
  
  // Calibrate gyroscope. The calibration must be at rest.
  // If you don't want calibrate, comment this line.
  mpu.calibrateGyro();

  // Set threshold sensivty. Default 3.
  // If you don't want use threshold, comment this line or set 0.
  mpu.setThreshold(3);
  
  // Motor driver setup
  pinMode(IN1, OUTPUT);
  pinMode(IN2, OUTPUT);
  pinMode(ENA, OUTPUT);
  pinMode(IN3, OUTPUT);
  pinMode(IN4, OUTPUT);
  pinMode(ENB, OUTPUT);

  // Encoder initialization
  EncoderInit();

  // PID setup
  myPID1.SetMode(AUTOMATIC);// PID is set to automatic mode
  myPID1.SetSampleTime(50);// PID sampling every 0.05 seconds
  myPID2.SetMode(AUTOMATIC);// PID is set to automatic mode
  myPID2.SetSampleTime(50);// PID sampling every 0.05 seconds
}

void loop()
{
  //Serial.print("Pulse:");
  //Serial.println(duration1);
  //Serial.print("Pulse:");
  //Serial.println(duration2);
  abs_duration1=abs(duration1);
  abs_duration2=abs(duration2);
  result1=myPID1.Compute();
  result2=myPID2.Compute();
  if(result1 && result2)
  {

    duration1, duration2 = 0; //Count clear, wait for the next count
    }
  timer = millis();
  Vector normGyro = mpu.readNormalizeGyro();
  Vector normAccel = mpu.readNormalizeAccel();
  
  if ( (millis()-range_timer) > 50){
    yaw = yaw+normGyro.ZAxis*(millis()-range_timer)*0.001;
    t.header.frame_id = world;
    t.child_frame_id = imu;
    t.transform.rotation.w = cos((yaw/2));
    t.transform.rotation.z = sin((yaw/2));
    t.transform.rotation.y = 0;
    t.transform.rotation.x = 0;
    t.header.stamp = nh.now();
    broadcaster.sendTransform(t); 

    range_timer = millis();
    }
    nh.spinOnce();
}

void EncoderInit()
{
  Direction1 = true;//default -> Forward
  Direction2 = true;
  pinMode(encoder0pinB,INPUT);
  attachInterrupt(1, wheelSpeed1, CHANGE);
  attachInterrupt(0, wheelSpeed2, CHANGE);
}

void wheelSpeed1()
{
  int Lstate1 = digitalRead(encoder0pinA);
  if((encoder0PinALast == LOW) && Lstate1==HIGH)
  {
    int val1 = digitalRead(encoder0pinB);
    if(val1 == LOW && Direction1)
    {
      Direction1 = false; //Reverse
    }
    else if(val1 == HIGH && !Direction1)
    {
      Direction1 = true;  //Forward
    }
  }
  encoder0PinALast = Lstate1;

  if(!Direction1){
    duration1--;
  }
  else{
    duration1++;
  }
}

void wheelSpeed2()
{
  int Lstate2 = digitalRead(encoder1pinA);
  if((encoder1PinALast == LOW) && Lstate2==HIGH)
  {
    int val2 = digitalRead(encoder1pinB);
    if(val2 == LOW && Direction2)
    {
      Direction2 = false; //Reverse
    }
    else if(val2 == HIGH && !Direction2)
    {
      Direction2 = true;  //Forward
    }
  }
  encoder1PinALast = Lstate2;

  if(!Direction2){
    duration2++;
  }
  else{
    duration2--;
  }
}

// Motor 1 command
void move_motor1()
{
    // Saturation: Max PWM = 255 and Min PWM = -255
    if (PWM1>255){
      PWM1 = 250;
    }

    else if(PWM1<-255){
      PWM1 = -250;
    }

     // PWM + Direction
     analogWrite(ENA,PWM1);
     digitalWrite(IN1,HIGH);
     digitalWrite(IN2,LOW);
}

// Motor 2 command
void move_motor2()
{
    // Saturation: Max PWM = 255 and Min PWM = -255
    if (PWM2>255){
      PWM2 = 250;
    }

    else if(PWM2<-255){
      PWM2 = -250;
    }

     // PWM + Direction
     analogWrite(ENB,PWM2);
     digitalWrite(IN3,HIGH);
     digitalWrite(IN4,LOW);
}

void calculate(double thetadot, double setspeed){
  
}

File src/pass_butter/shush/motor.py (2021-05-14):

__author__ = 'ZJAllen'

from shush.board import Board, s1, gpio
from shush.drivers import tmc5160_reg as reg
import time

from shush.params import Ramp as ramp


class Motor(Board):

    def __init__(self, motor: int):
        # Setting the CS and enable pins according to the motor number called

        if motor == 0:
            self.chip_select = s1.m0_cs
            self.enable = s1.m0_enable

        # Initially apply default settings.
        # These can be configured at any time.
        self.default_settings()

    def enable_motor(self):
        # Pull Enable pin LOW to enable motor

        gpio.output(self.enable, gpio.LOW)

    def disable_motor(self):
        # Pull Enable pin HIGH to disable motor

        gpio.output(self.enable, gpio.HIGH)

    def default_settings(self):
        # Set default motor parameters

        # MULTISTEP_FILT = 1, EN_PWM_MODE = 1 enables stealthChop
        self.write(reg.GCONF, 0x0000000C)
        # TOFF = 3, HSTRT = 4, HEND = 1, TBL = 2, CHM = 0 (spreadCycle)
        self.write(reg.CHOPCONF, 0x000100C3)
        # IHOLD = 2, IRUN = 15 (max current), IHOLDDELAY = 8
        self.write(reg.IHOLD_IRUN, 0x00080F02)
        # TPOWERDOWN = 10: Delay before powerdown in standstill
        self.write(reg.TPOWERDOWN, 0x0000000A)
        # TPWMTHRS = 500
        self.write(reg.TPWMTHRS, 0x000001F4)

        self.reset_ramp_defaults()

        # Position mode
        self.write(reg.RAMPMODE, 0)
        # Set current position to 0
        self.write(reg.XACTUAL, 0)
        # Set XTARGET to 0, which holds the motor at the current position
        self.write(reg.XTARGET, 0)

    # TODO: add some more functionality...
    # Add stallGuard + coolStep (datasheet page 52)

    def set_VSTART(self, value: int):
        self.write(reg.VSTART, value)
        ramp.VSTART = value

    def set_A1(self, value: int):
        self.write(reg.A1, value)
        ramp.A1 = value

    def set_V1(self, value: int):
        self.write(reg.V1, value)
        ramp.V1 = value

    def set_AMAX(self, value: int):
        self.write(reg.AMAX, value)
        ramp.AMAX = value

    def set_VMAX(self, value: int):
        self.write(reg.VMAX, value)
        ramp.VMAX = value

    def set_DMAX(self, value: int):
        self.write(reg.DMAX, value)
        ramp.DMAX = value

    def set_D1(self, value: int):
        self.write(reg.D1, value)
        ramp.D1 = value

    def set_VSTOP(self, value: int):
        self.write(reg.VSTOP, value)
        ramp.VSTOP = value

    def write_ramp_params(self):
        self.set_VSTART(ramp.VSTART)
        self.set_A1(ramp.A1)
        self.set_V1(ramp.V1)
        self.set_AMAX(ramp.AMAX)
        self.set_VMAX(ramp.VMAX)
        self.set_DMAX(ramp.DMAX)
        self.set_D1(ramp.D1)
        self.set_VSTOP(ramp.VSTOP)

    def reset_ramp_defaults(self):
        ramp.VSTART = 1
        ramp.A1 = 25000
        ramp.V1 = 250000
        ramp.AMAX = 5000
        ramp.VMAX = 1000000
        ramp.DMAX = 5000
        ramp.D1 = 50000
        ramp.VSTOP = 10

        self.write_ramp_params()

    def enable_switch(self, direction: int):
        # Configure limit switch.
        # See datasheet for limit switch config default_settings

        # Initialize list
        setting_array = [0] * 12

        # en_softstop = 1
        setting_array[0] = 1

        if direction == 1:
            setting_array[6] = 1     # latch_l_active = 1
            setting_array[11] = 1    # stop_l_enable = 1
            error = False
        elif direction == 2:
            setting_array[4] = 1     # latch_r_active = 1
            setting_array[10] = 1    # stop_r_enable = 1
            error = False
        else:
            print("Not a valid input! Please use 1 (left), or 2 (right).")
            error = True

        if not error:
            # Create binary string, to be correctly sent over SPI
            switch_settings = int(''.join(str(i) for i in setting_array), 2)
            self.write(reg.SWMODE, switch_settings)

    def get_position(self) -> int:
        # Returns the current position of the motor relative to Home (0)

        current_position = self.read(reg.XACTUAL)

        # Convert 2's complement to get signed number
        current_position = self.twos_comp(current_position)

        return current_position

    def get_latched_position(self) -> int:
        # Returns the latched position when using limit switches.

        latched_position = self.read(reg.XLATCH)

        # Convert 2's complement to get signed number
        latched_position = self.twos_comp(latched_position)

        return latched_position

    def get_velocity(self) -> int:
        # Returns the current velocity of the motor (+ or -)

        current_velocity = self.read(reg.VACTUAL)

        # Convert 2's complement to get signed number
        # VACTUAL is valid for +-(2^23)-1, so 24 bits
        # 24 bits optional argument
        current_velocity = self.twos_comp(current_velocity, 24)

        return current_velocity

    def go_to(self, position: int):
        # Move to an absolute position relative to Home (0).

        self.position_mode()

        self.write_ramp_params()

        # Position range is from -2^31 to +(2^31)-1
        maximum_position = (2**31) - 1
        minimum_position = -(2**31)

        # Check if position is within bounds
        if position > maximum_position:
            position = maximum_position
            print("Maximum position reached! Stopped at max value.")
        elif position < minimum_position:
            position = minimum_position
            print("Minimum position reached! Stopped at min value.")

        self.write(reg.XTARGET, position)

    def calibrate_home(self, direction: int):
        # Calibrate home by driving motor to limit switch.
        # This is position-based rather than velocity based
        # Direction: use 1 for left, 2 for right

        self.enable_switch(direction)

        # If the switch is active, move away from the switch until inactive
        self.get_ramp_status()

        switch_pressed = int(self.get_ramp_status.status_stop_l)

        if direction == 1:
            error = False

            switch_pressed = int(self.get_ramp_status.status_stop_l)

            if switch_pressed == 1:

                # Move away from switch
                self.go_to(512000)

                while switch_pressed == 1:
                    self.get_ramp_status()
                    switch_pressed = int(self.get_ramp_status.status_stop_l)

        elif direction == 2:
            error = False

            switch_pressed = int(self.get_ramp_status.status_stop_r)

            if switch_pressed == 1:

                # Move away from switch
                self.go_to(-512000)

                while switch_pressed == 1:
                    self.get_ramp_status()
                    switch_pressed = int(self.get_ramp_status.status_stop_r)
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

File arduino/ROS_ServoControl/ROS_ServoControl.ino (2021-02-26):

/*
 * rosserial Servo Control Example
 *
 * This sketch demonstrates the control of hobby R/C servos
 * using ROS and the arduiono
 * 
 * For the full tutorial write up, visit
 * www.ros.org/wiki/rosserial_arduino_demos
 *
 * For more information on the Arduino Servo Library
 * Checkout :
 * http://www.arduino.cc/en/Reference/Servo
 */

#if (ARDUINO >= 100)
 #include <Arduino.h>
#else
 #include <WProgram.h>
#endif

#include <Servo.h> 
#include <ros.h>
#include <std_msgs/UInt16.h>

ros::NodeHandle  nh;

Servo servo;

void servo_cb( const std_msgs::UInt16& cmd_msg){
  servo.write(cmd_msg.data); //set servo angle, should be from 0-180  
  digitalWrite(13, HIGH-digitalRead(13));  //toggle led  
}


ros::Subscriber<std_msgs::UInt16> sub("servo", servo_cb);

void setup(){
  pinMode(13, OUTPUT);

  nh.initNode();
  nh.subscribe(sub);
  
  servo.attach(3); //attach it to pin 3
}

void loop(){
  nh.spinOnce();
  delay(1);
}

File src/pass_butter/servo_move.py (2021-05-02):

from adafruit_servokit import ServoKit
import board
import busio
import time

# On the Jetson Nano
# Bus 0 (pins 28,27) is board SCL_1, SDA_1 in the jetson board definition file
# Bus 1 (pins 5, 3) is board SCL, SDA in the jetson definition file
# Default is to Bus 1; We are using Bus 0, so we need to construct the busio first ...
print("Initializing Servos")
i2c_bus0=(busio.I2C(board.SCL_1, board.SDA_1))
print("Initializing ServoKit")
kit = ServoKit(channels=16, i2c=i2c_bus0)
# kit[0] is the bottom servo
# kit[1] is the top servo
print("Done initializing")

def up():
    kit.servo[0].angle=180
    kit.servo[1].angle=180
    kit.servo[2].angle=0
    kit.servo[3].angle=0

def down():
    kit.servo[0].angle=0
    kit.servo[1].angle=145
    kit.servo[2].angle=180
    kit.servo[3].angle=40

def wave():
    kit.servo[0].angle=180
    kit.servo[1].angle=180
    kit.servo[2].angle=0
    kit.servo[3].angle=0
    time.sleep(.5)
    kit.servo[2].angle=40
    kit.servo[3].angle=120
    time.sleep(.3)
    kit.servo[3].angle=40
    time.sleep(.3)
    kit.servo[3].angle=120
    time.sleep(.3)
    kit.servo[3].angle=40
    time.sleep(.3)
    kit.servo[3].angle=120
    time.sleep(.3)
    kit.servo[3].angle=40
    time.sleep(.3)
    kit.servo[3].angle=120
    time.sleep(.3)

#kit.servo[0].angle=0 #180 #smaller cw, larger ccw
#kit.servo[1].angle=180 #smaller cw larger ccw --down setpoint at 150, straight at 105, back at 180.
#kit.servo[3].angle=0 #100 straight 40 down
#kit.servo[2].angle=180 #0 up 180 up

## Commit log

2021-02-26 Basic control of servo connected to Arduino using ROS.
2021-04-05 Create motor_control.ino
    Arduino motor control and sensor
2021-04-28 pwm arm control.
2021-04-28 first working servo arm.
2021-04-30 refactor motor control arduino sketch with bot pin numbers.
2021-05-01 working arm with some cool helper functions.
2021-05-01 added arduino sketch for position control.
2021-05-01 movement calibration.
2021-05-02 running on jetson.
2021-05-02 working roslaunch and such on jetson.
2021-05-14 Added schematics and stepper driver code
    [OldSchematic.fzz, Schematic.fzz]
2021-06-07 documentation and background material for everything.
    [BOM.xlsx, Bracket v1.stl, OldSchematic.fzz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]
